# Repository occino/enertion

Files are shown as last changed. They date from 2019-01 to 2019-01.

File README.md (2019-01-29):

# "Raptor 2.1 GTX" | R-SPEC DRIVE | FOCBOX Unity | 12S3P VTC5 | 3D printed custom enclosure

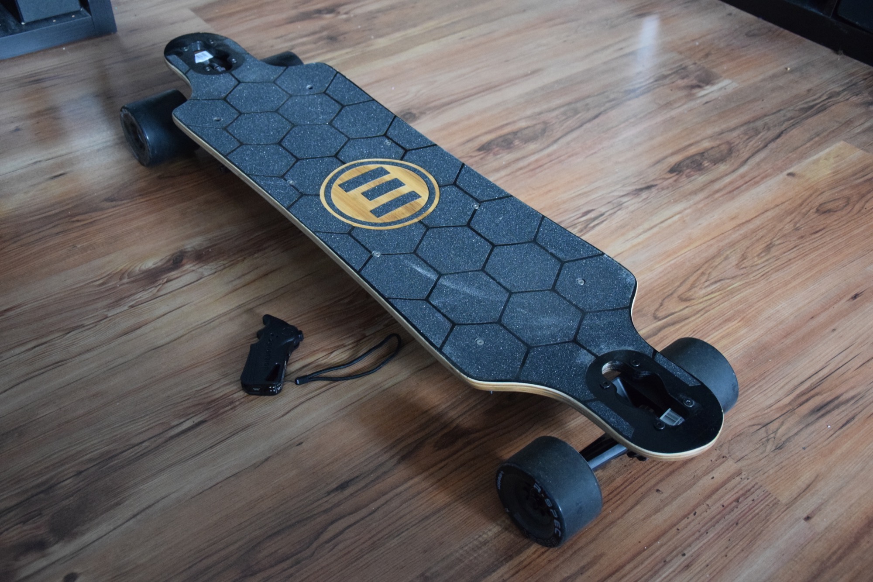
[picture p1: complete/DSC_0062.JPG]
Complete1


**Hi guys,**

I'm Nico from Berlin, Germany and I'm building electric longboards since two years now. I would like to share with you my latest and easiest build which is technically a Raptor 2.1 with at GTX deck. I'm also motivated to write this post because of the **Enertion R-SPEC DRIVE KIT | Best Build Competition** [[link](https://www.electric-skateboard.builders/t/enertion-r-spec-drive-kit-best-build-competition-win-cash-back/ "Enertion")].

## Specs & features:

* R-SPEC DRIVE KIT w/ 90mm wheels [[link](https://www.enertionboards.com/electric-skateboard-direct-drive-hub-motor-kit-r-spec/ "R-SPEC DRIVE KIT")]
* FOCBOX UNITY ESC [[link](https://www.enertionboards.com/focbox-speed-controller/focbox-unity-dual-motor-foc-controller-esc/ "FOCBOX UNITY ESC")]
* Evolve GTX deck [[link](https://evolveskateboardsusa.com/products/deck-bamboo-gtx "Evolve")]
* Custom 12S3P battery pack w/ VTC5 + BMS [[link](https://eu.nkon.nl/sony-us18650vtc5-flat-top.html "eu.nkon.nl"), [link](https://www.aliexpress.com/item/BMS-6S-7S-8S-9S-10S-11S-12S-13S-4-2V-25A-Adjustable-BMS-Lithium-Li/32931097519.html "BMS")]
* 3D printed custom enclosure + PVC bottom plate [[link](https://www.thingiverse.com/thing:3382660 "Thingiverse")]
* Enertion Nano-X 2.4Ghz Controller [[link](https://www.enertionboards.com/electric-skateboard-parts/nano-x-enertion-2-4ghz-controller/ "Remote")]
* Voltage display [[link](https://de.aliexpress.com/item/0-36-DC0-100V-LED-Mini-Digital-Voltmeter-Blue-red-green-LED-Display-Volt-Meter/32817252098.html "link")]
* USB charging port module [[link](https://de.aliexpress.com/item/LM2596HV-5V-DC-DC-Step-Down-Buck-Converter-Module-9V-12V-24V-36V-48V-to-5V/32831931798.html "link")]
* Loop key

## GTX deck
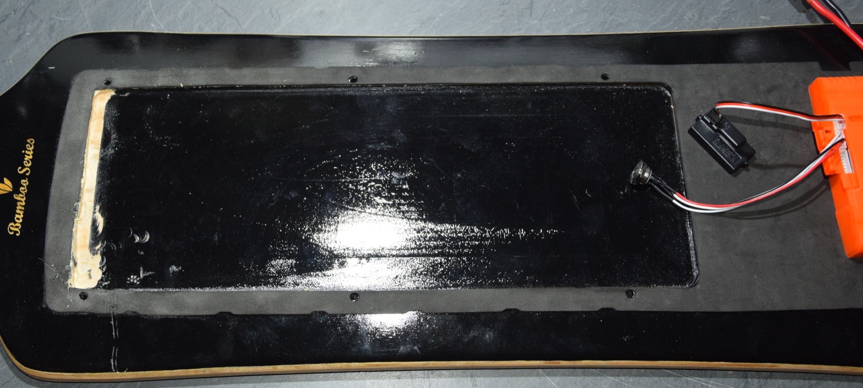
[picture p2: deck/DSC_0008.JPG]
GTX1

The GTX deck by evolve is perfectly suited in my opinion because it comes already with a notch for the battery pack. Furthermore it's flexible and looks nice.

In order to use a 10S4P battery, the notch had to be enlarged by about 1 cm. I used the original screw holes to mount the enclosure.

## Enclosure
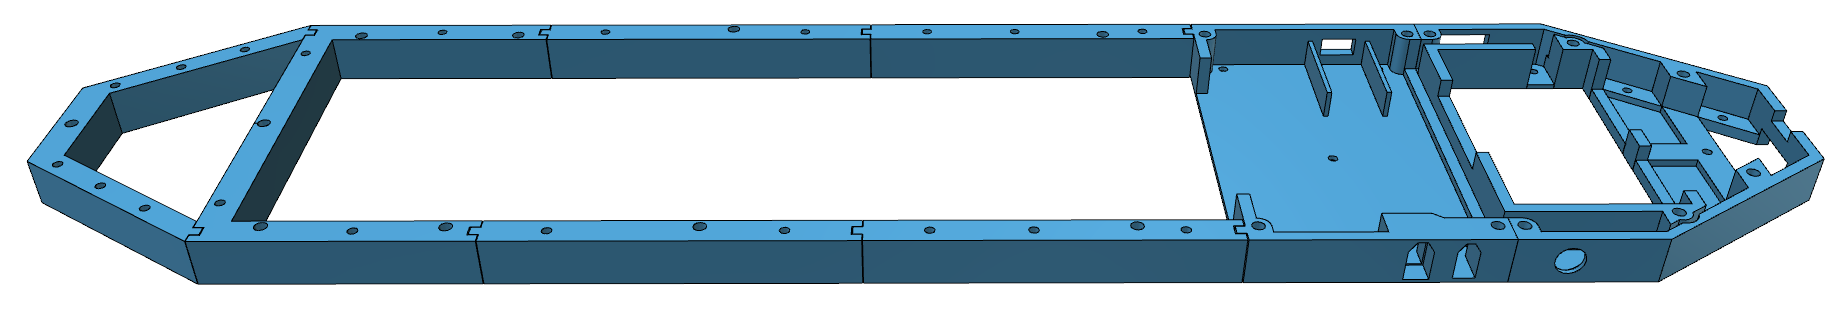
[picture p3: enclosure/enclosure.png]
Enclosure1

The enclosure is a modular 3D printed frame with a PVC plate underneath. Due to the dimension limits of 3D printing, I decided to design a modular system which can be printed in multiple parts. To ensure water resistence, I used a *tongue and groove* technique which makes the enclosure flexible as well. I also used sponge rubber between deck and enclosure as well as between PVC plate and enclosure.
You can find all parts on [thingiverse](https://www.thingiverse.com/thing:3382660 "Thingiverse").

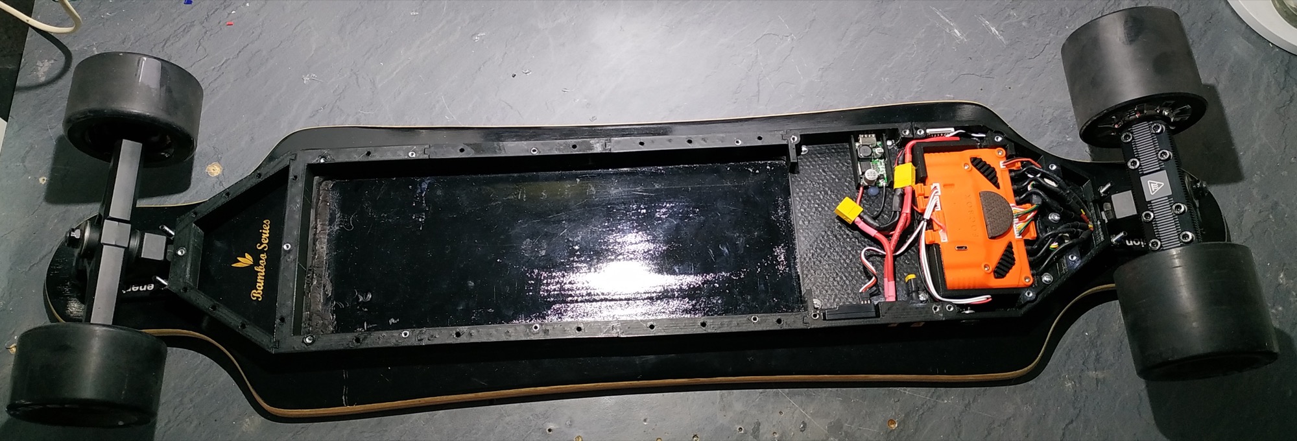
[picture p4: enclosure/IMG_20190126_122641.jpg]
Enclosure2


### Mounting
In order to mount the PVC plate underneath, I glued M4 threaded sleeves (5mm x 18mm) ([link](http://www.lignoshop.de/gewindehuelse-stahl-m4-5mm-37811022000.html "link")) into the parts as you can see in the picture below. This way I could use proper thread screws. The threaded sleeves pass through the entire material. This allowed the deck to be screwed on from both sides. This makes the construction pretty strong. 

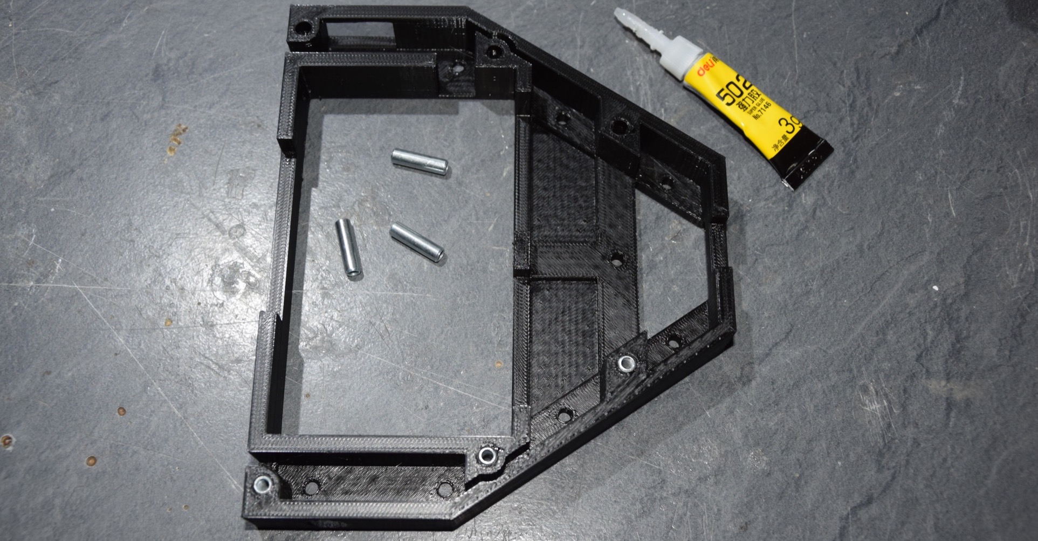
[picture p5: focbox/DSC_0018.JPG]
Enclosure3


### FOCBOX UNITY case
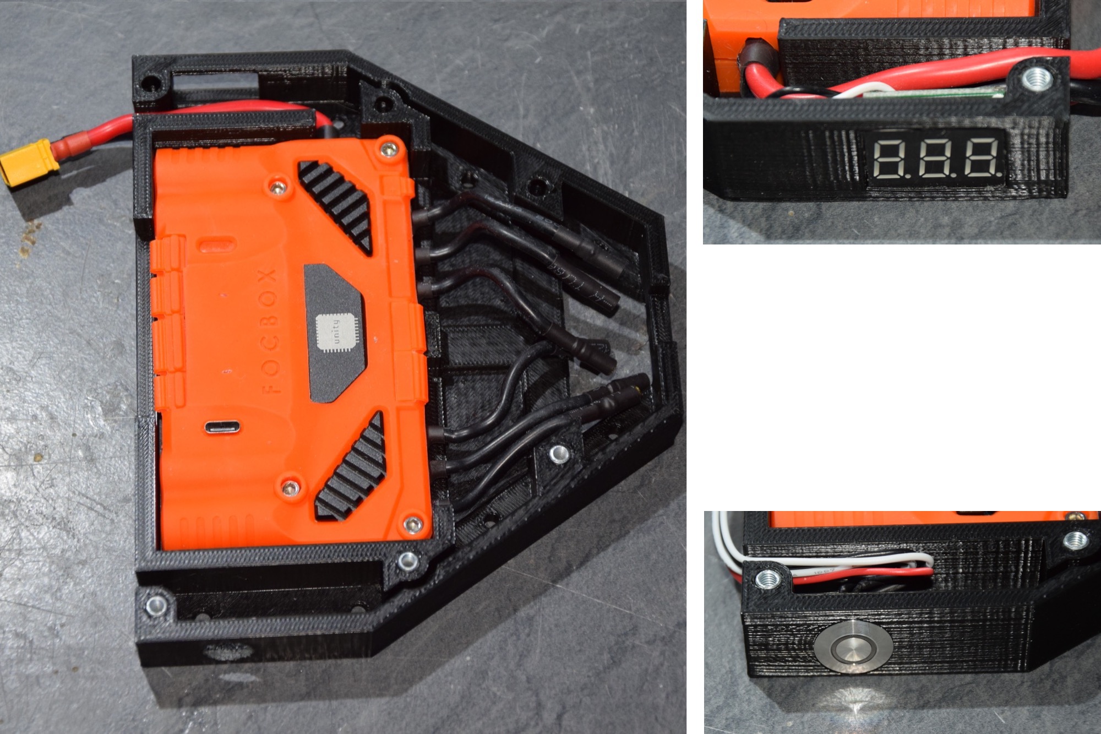
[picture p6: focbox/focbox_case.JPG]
FOCBOX1

The rear part of the enclosure contains the FOCBOX UNITY as well as a battery voltage display  and the power switch provided by enertion. The voltage display is powered by the CAN bus port (5V, GND) and the measuring wire is connected to the BATT+ pin of the AUX port. The FOCBOX sits tightly into the compartment, so there is no need to mount it with screws.

### Connector box
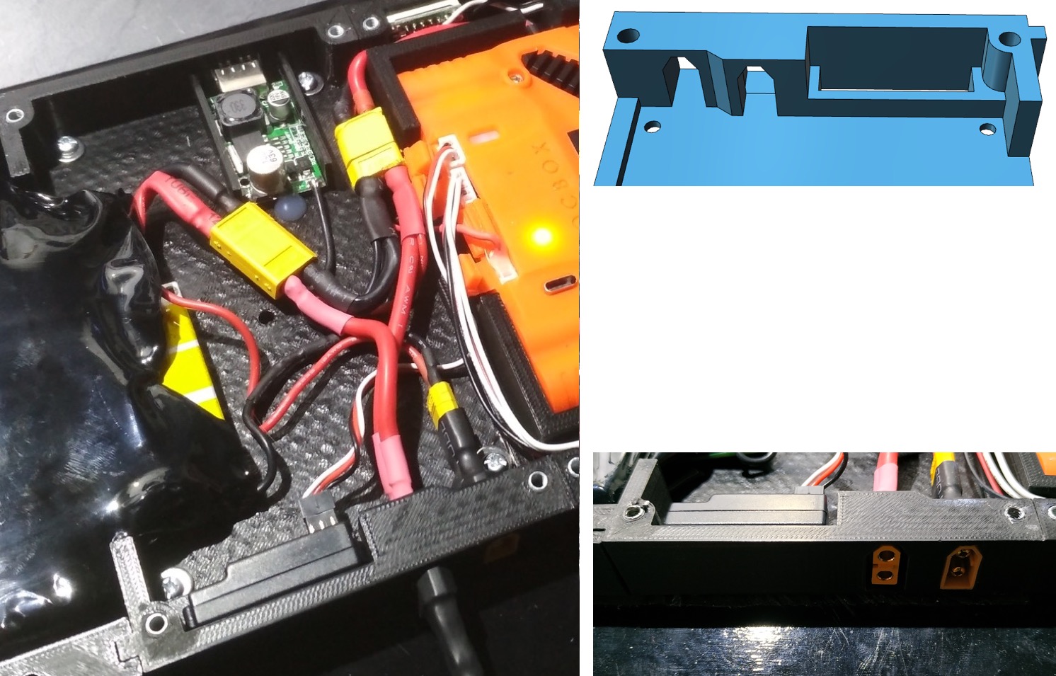
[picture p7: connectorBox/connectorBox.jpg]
ConnectorBox1

The connector box is the middle part of the enclosure and contains receiver, 3A USB charging module (LM2596HV), XT60 charging port, XT60 key loop and all wiring. The charging port is connected to the BMS via XT30 in order to change the battery easily. The receiver of the Enertion Nano-X 2.4Ghz Controller fits perfectly in a small compartment and doesn't need to be srewed down.

### Battery pack (12S3P, Sony Konion VTC5)
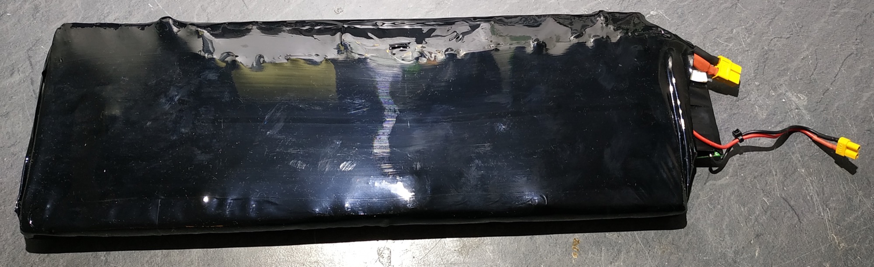
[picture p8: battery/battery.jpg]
Battery1

12S3P or 10S4P? I chose both variants. 12S for more fun and 10S for more range. For the 12S3P pack I used 36 **Sony Konion US18650VTC5 cells 2600mAh** with a total capacity of 336Wh. I paid 128€ for 36 VTC5 cells on [eu.nkon.nl](https://eu.nkon.nl/ "eu.nkon.nl"). 36 VTC6 cells with 3000mAh would have cost 207€ for additonal 53Wh. Range is not that important to me, so I took the cheaper option.

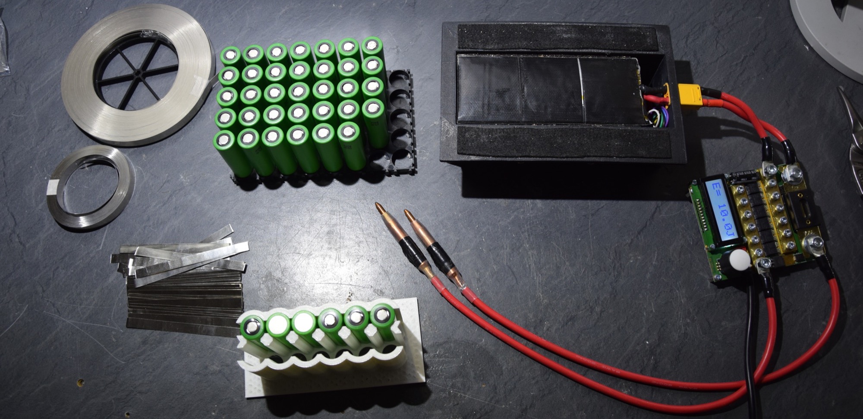
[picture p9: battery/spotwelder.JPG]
Battery1


For spotwelding, I used the amazing kWeld by [keenlab](https://www.keenlab.de/ "keenlab") powered by a high discharge lipo. The nickel strips are pure nickel  (8mm x 0.3mm). I made some tests and figured out that they can easily handle 25A. In order to archive the full rated 90A of the cells, I used 4 layers of nickel (pyramid technique) at the S-transitions to be on the safe side.

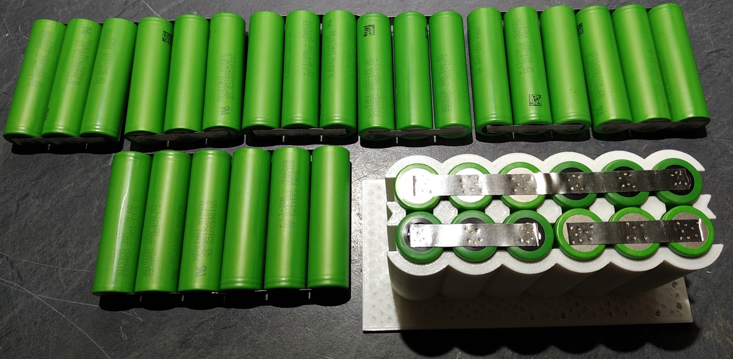
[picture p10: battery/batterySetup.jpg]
Battery2


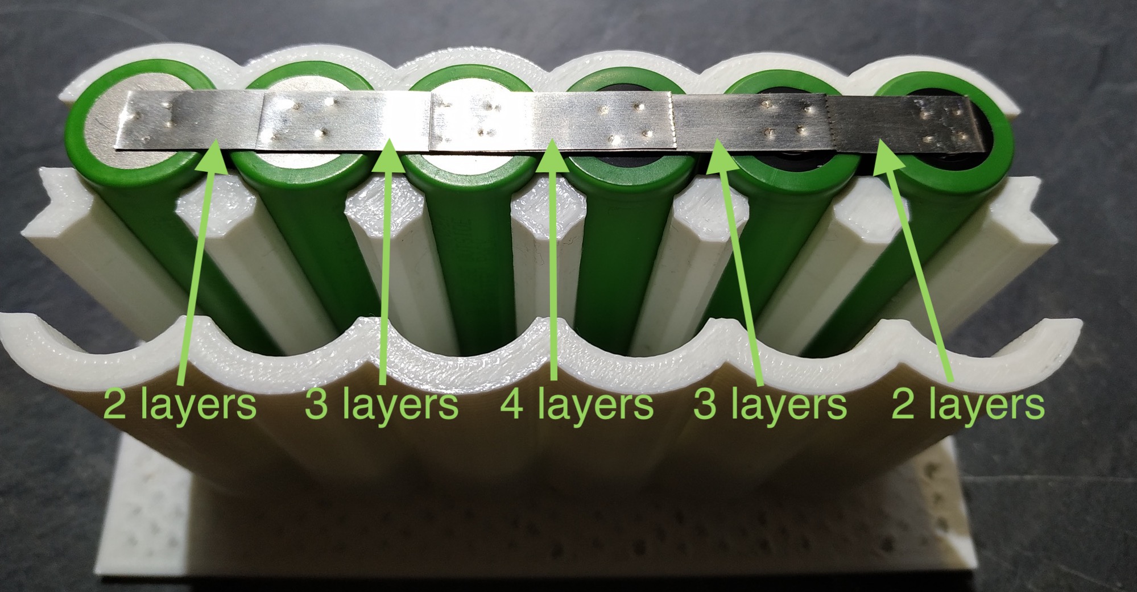
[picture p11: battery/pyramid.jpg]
Battery3


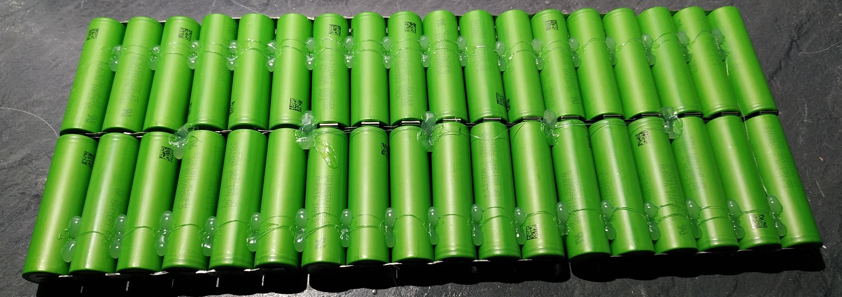
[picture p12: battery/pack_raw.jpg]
Battery4


The BMS is a cheap 13S circuit usable for 12S as well. It is only used for charging and not for discharging. To prevent the battery from over discharge, I used the cut off setting of the FOCBOX UNITY.
As I mentioned before, I would like to use 12S3P and 10S4P battery packs in the battery compartment. In order to get the same dimensions, I printed a 2x2 dummy cell construction as your can see on the picture below.

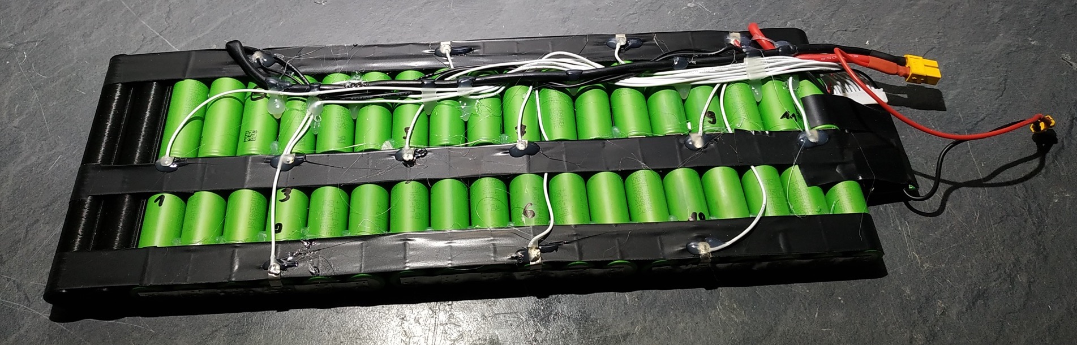
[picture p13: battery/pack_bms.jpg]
Battery5


After adding all the wires, I added felt pads on all edges which should absorb shocks and keep the pack tight in the battery compartment.

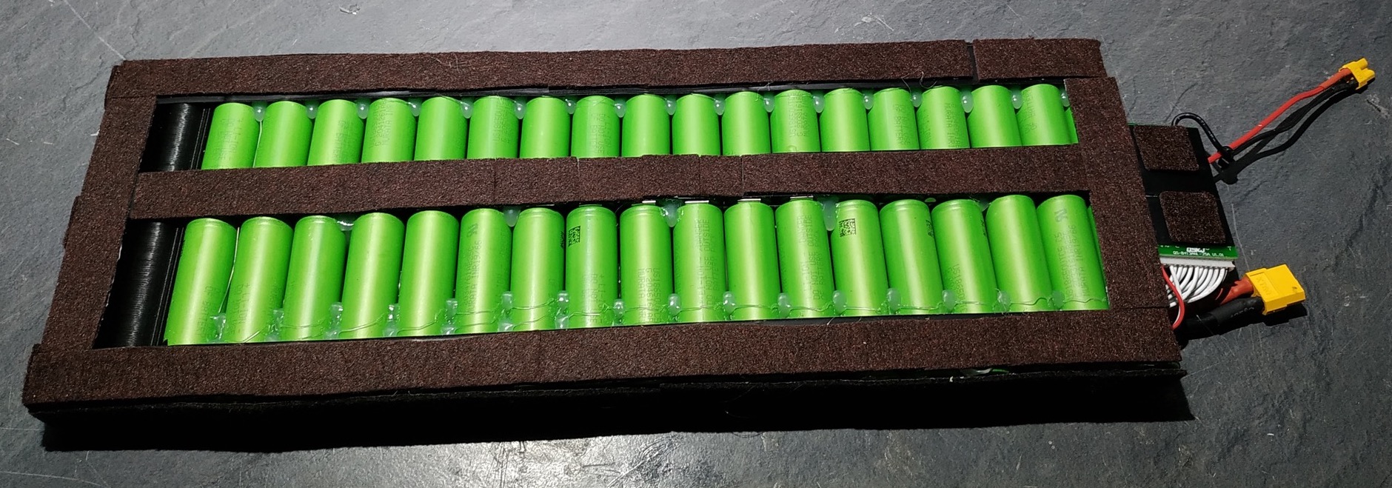
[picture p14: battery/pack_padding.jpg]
Battery6


Finally I used a 200mm shrink tube and a hot air gun to close the battery pack.

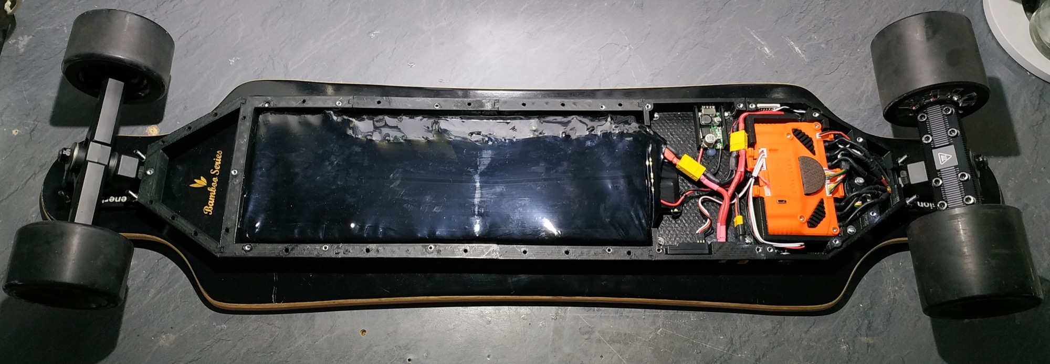
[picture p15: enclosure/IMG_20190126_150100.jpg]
Battery7


After inserting the battery and connecting the XT60 and XT30, the only thing left was the bottom plate.

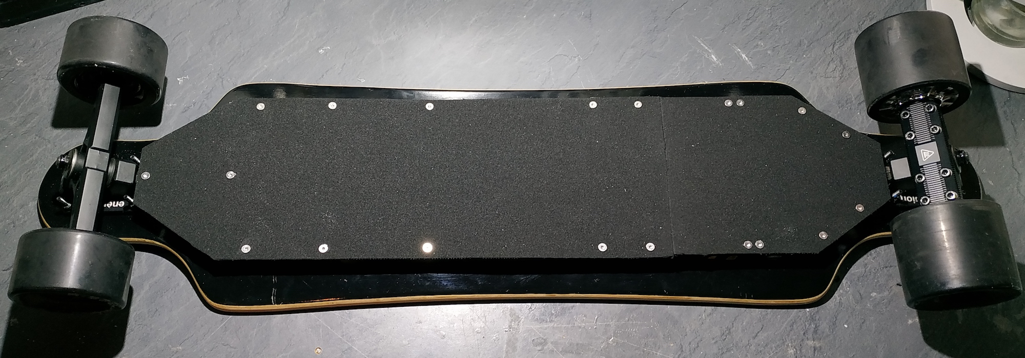
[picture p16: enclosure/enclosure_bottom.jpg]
Battery8


That's it. Just an easy, modular build :).

What do you think? Any suggestions for improvements?

If you have any questions please feel free to drop a message.

Cheers, Nico

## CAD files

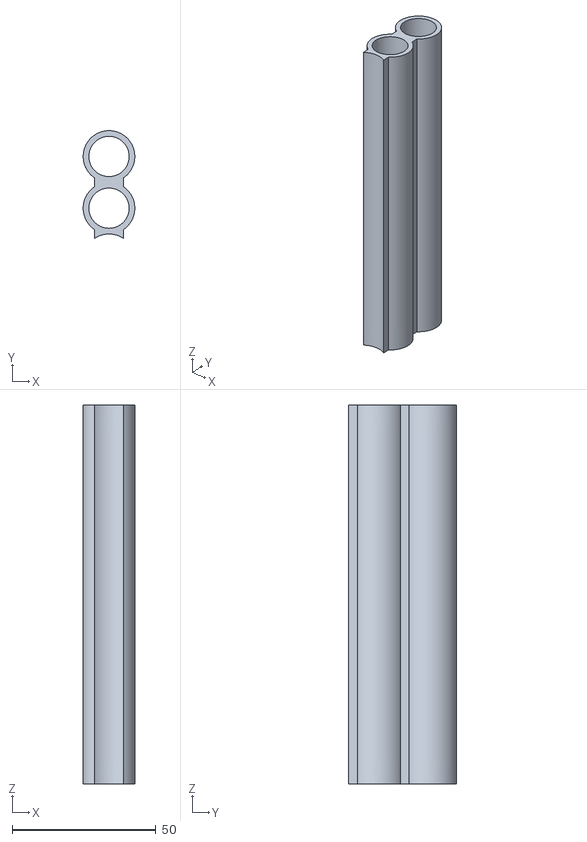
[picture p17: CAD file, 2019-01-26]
3D_parts/2x2CellDummy.stl
18.0 x 37.5 x 132.0

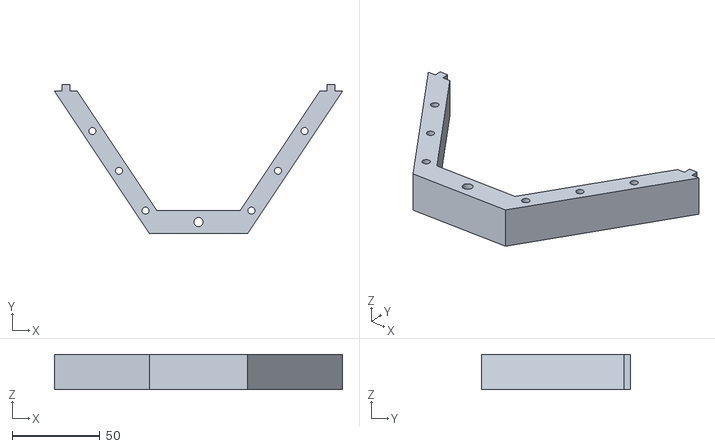
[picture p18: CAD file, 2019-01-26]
3D_parts/frame_part1.stl
164.0 x 84.8 x 20.0

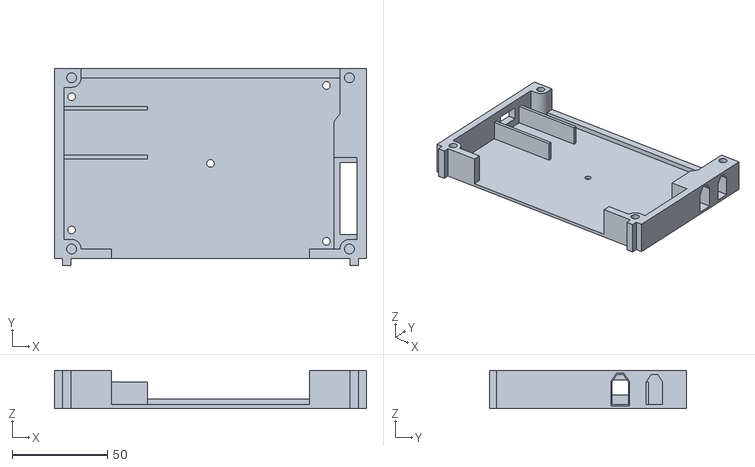
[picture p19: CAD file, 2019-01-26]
3D_parts/connectorBox.stl
164.0 x 103.8 x 20.0

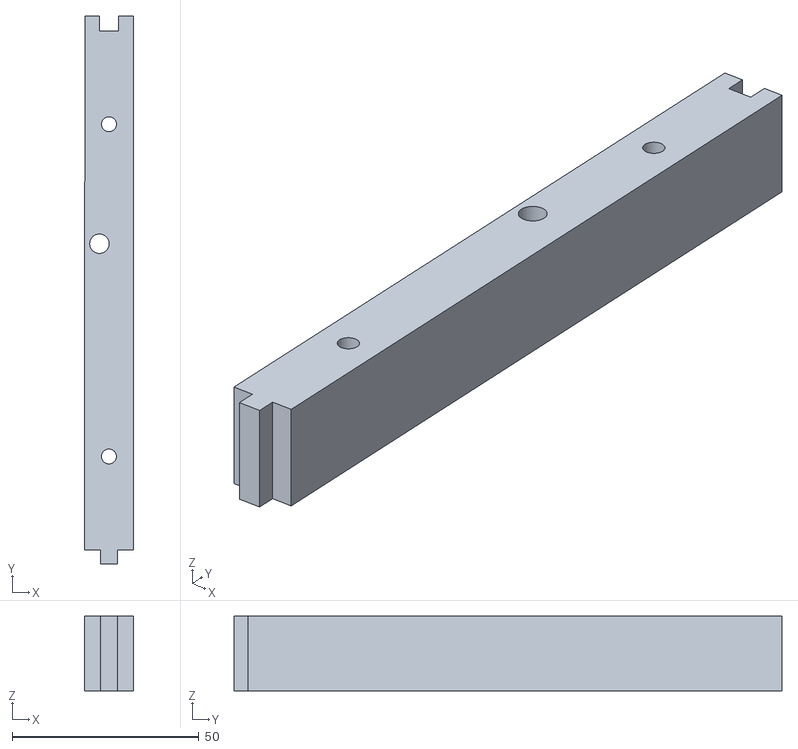
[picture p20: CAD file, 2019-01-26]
3D_parts/frame_part3.stl
13.0 x 146.8 x 20.0

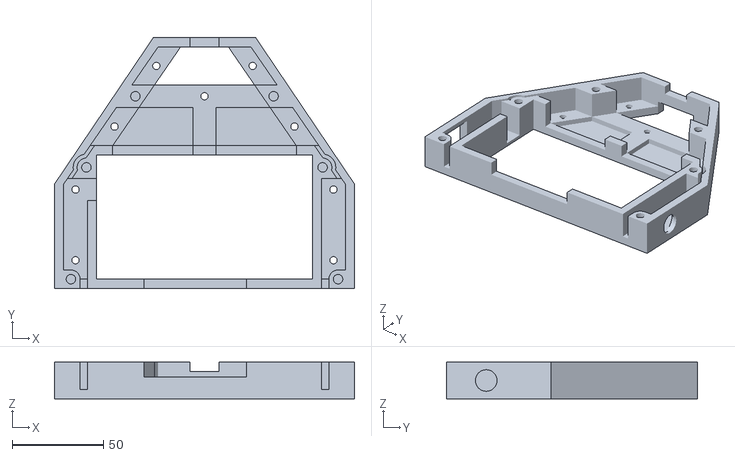
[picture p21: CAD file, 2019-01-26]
3D_parts/focboxCase.stl
164.0 x 137.0 x 20.0

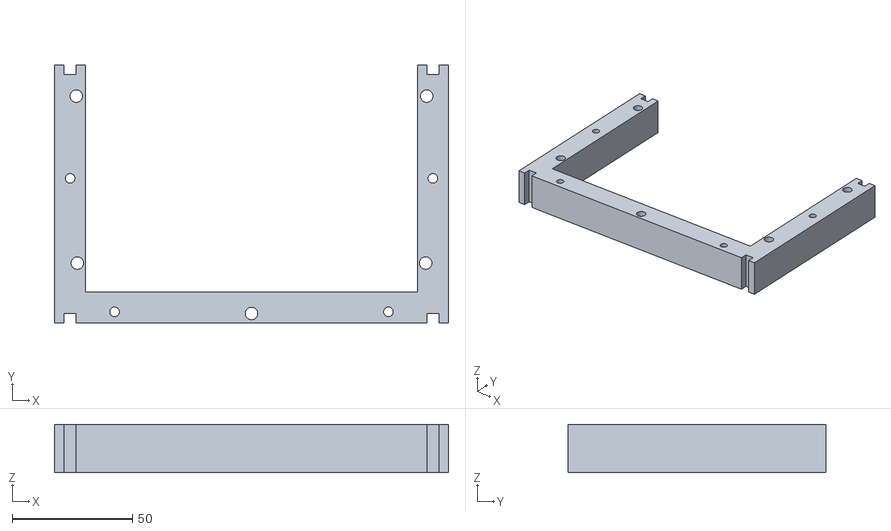
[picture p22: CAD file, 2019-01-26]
3D_parts/frame_part2.stl
164.0 x 107.5 x 20.0

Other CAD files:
3D_parts/frame_part4.stl

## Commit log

2019-01-26 enclosure replacement
2019-01-26 battery done
2019-01-26 bottom plate
